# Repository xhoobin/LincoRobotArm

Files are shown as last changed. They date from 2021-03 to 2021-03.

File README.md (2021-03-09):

# tinco桌面机械臂

tinco桌面机械臂设计上易于3D打印，所需零件少。

此仓库包含3D设计图纸、STL 3D打印模型、材料清单、固件

Q群:624506541

## 打印参数

材料 pla 

层高 0.2

填充率 20%

## 样品照片

视频：https://www.bilibili.com/video/BV1D5411N7zT/

视频：https://www.bilibili.com/video/BV18U4y1p7vp

视频：https://www.bilibili.com/video/BV1Gf4y1z7et



## 零件清单

机械部分物料:

轴承钢6806ZZ          (30 * 42 * 7)      3

轴承钢6800ZZ          (10 * 19 * 5)      2

轴承钢6803ZZ           (17 * 26 * 5)     4

轴承钢MR104ZZ        (4 * 10 * 4)       8

2gt同步带                                 1米

m3*18沉孔螺丝                             8     (注意:要用沉孔螺丝)
m3*22螺丝                                   1

m3*10螺丝                                   12

还有胶水(粘轴承用,只在受力小的地方使用胶水,主副臂底座轴承则由打印的螺纹螺帽固定,非常结实)

 电气部分:

 ramps1.4                                      1

a4988驱动板                                  3

mega2560主板                               1 

限位微动开关SS-5GL                       2

12V10A电源                                   1

42步进电机                                    3

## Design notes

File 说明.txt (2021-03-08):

请按给的打印件原本的方向打印(可以保证表面光洁度),安装还是非常容易的 ,后续会推出安装视频,还有调试试频.固件

打印参数
材料 pla 
层高 0.2
填充率 20%

Q群:624506541
linco桌面机械臂

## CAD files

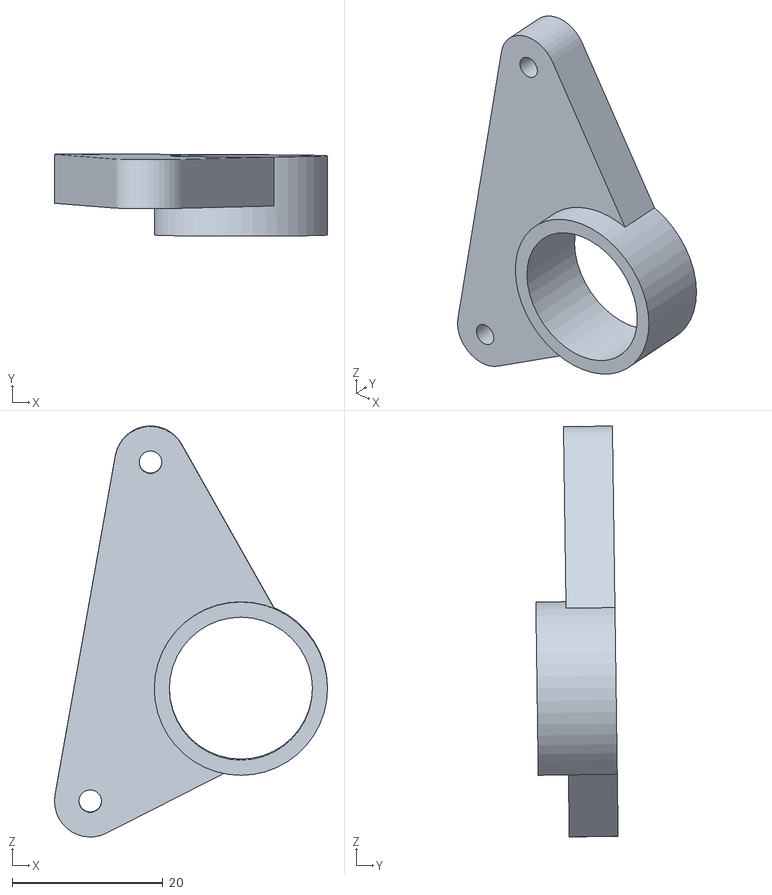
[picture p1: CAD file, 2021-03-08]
打印件/出错/三角.STL
36.2 x 10.9 x 54.6

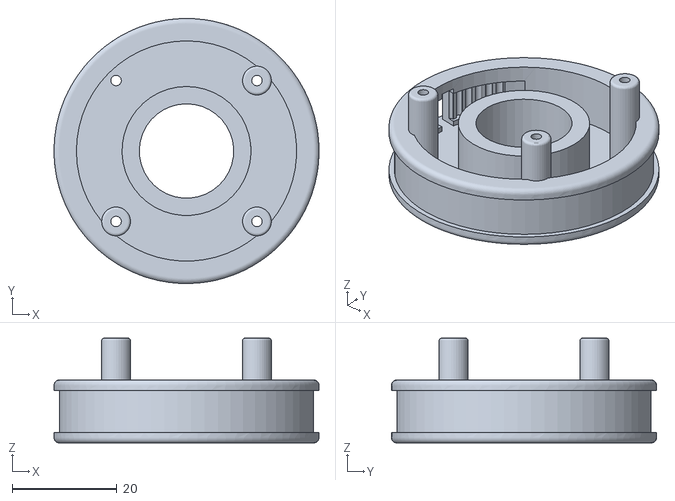
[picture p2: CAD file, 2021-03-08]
打印件/大部件/底轮.STL
50.5 x 50.5 x 20.0

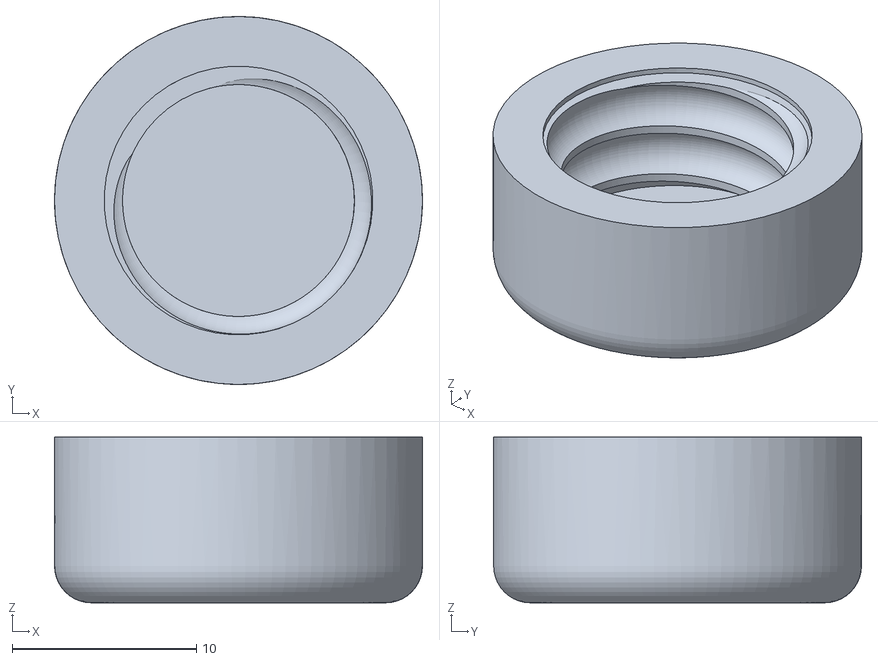
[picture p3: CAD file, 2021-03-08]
打印件/小部件/主臂5.STL
20.0 x 20.0 x 9.00

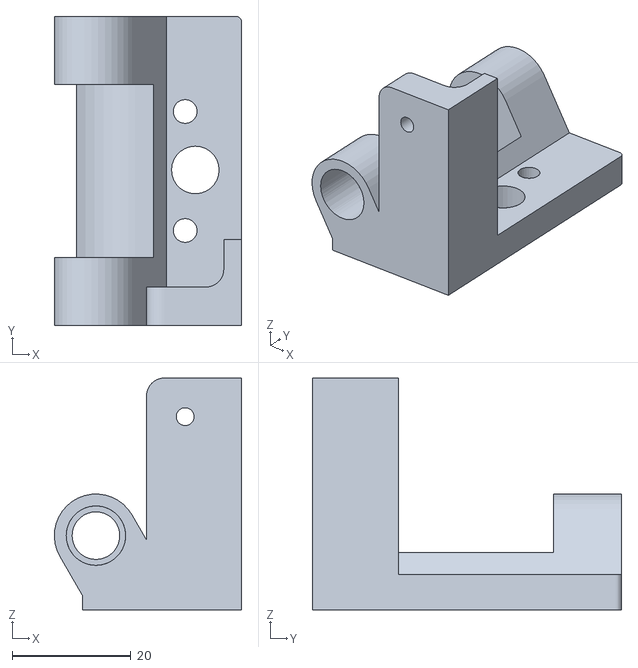
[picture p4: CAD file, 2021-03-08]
打印件/效应器改.STL
31.5 x 52.0 x 39.0

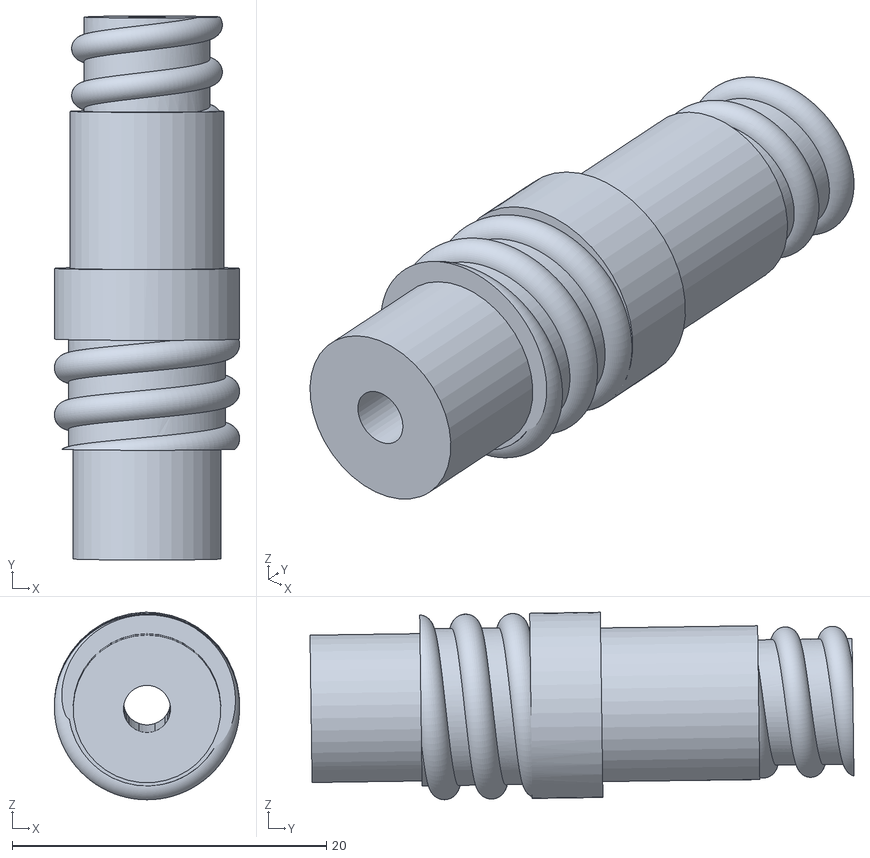
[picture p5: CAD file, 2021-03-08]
打印件/出错/轴.STL
11.8 x 34.6 x 11.9

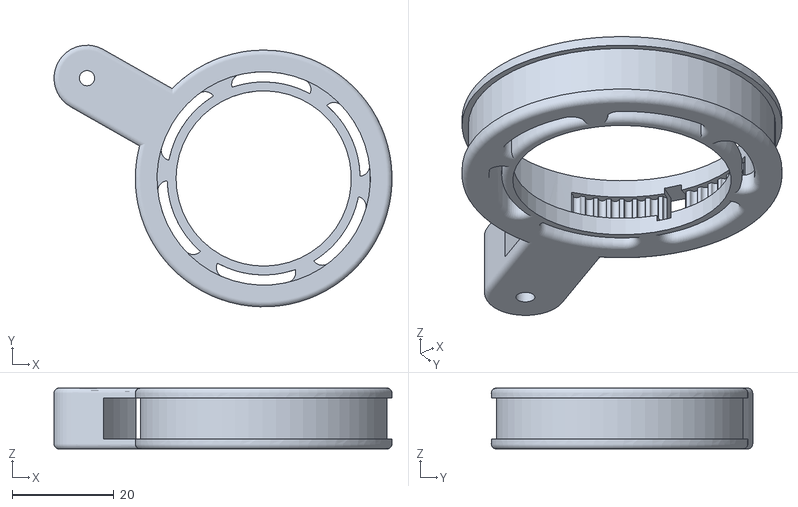
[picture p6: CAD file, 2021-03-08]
打印件/大部件/前轮.STL
66.6 x 51.5 x 12.0

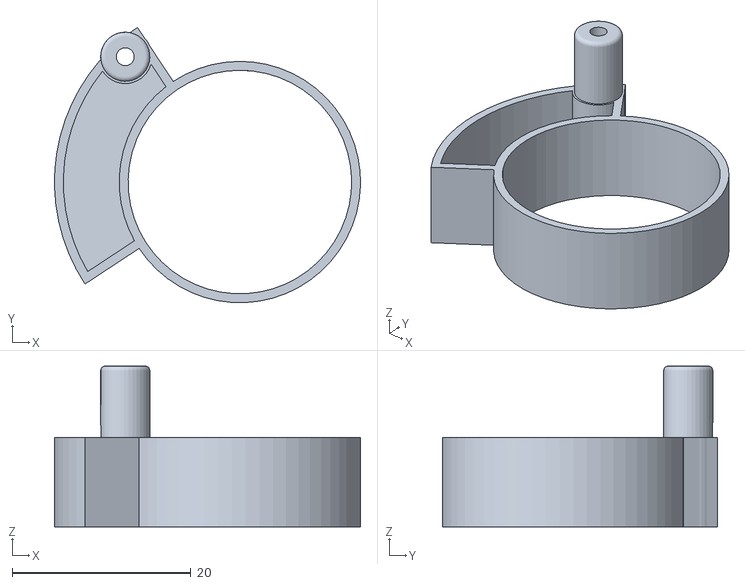
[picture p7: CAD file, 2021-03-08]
打印件/小部件/底轮卡.STL
34.2 x 30.8 x 18.0

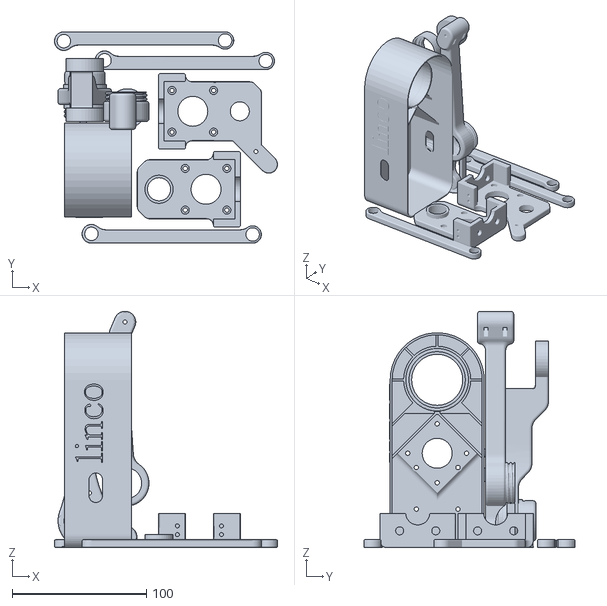
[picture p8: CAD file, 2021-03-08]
打印件/盘2.STL
166.0 x 157.4 x 176.0

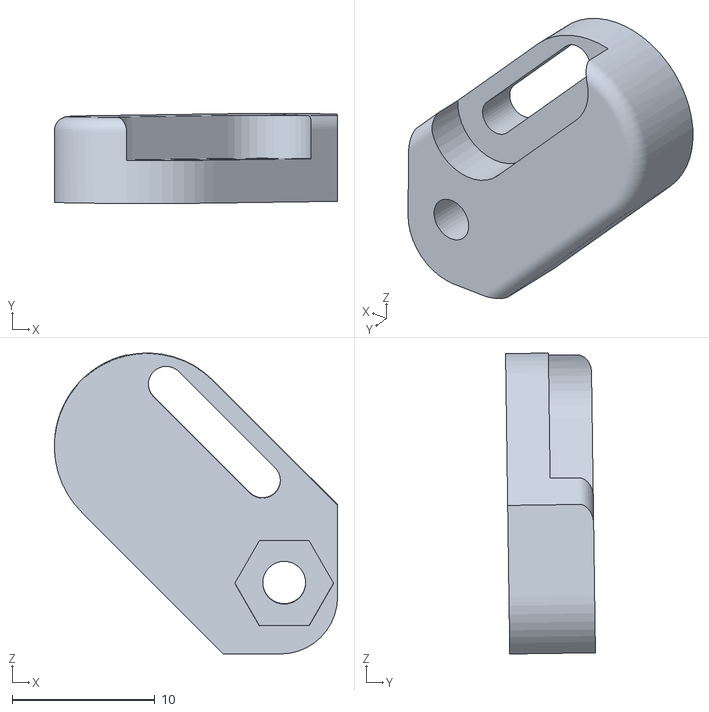
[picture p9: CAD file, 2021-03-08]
打印件/出错/限位固定.STL
19.8 x 6.29 x 21.1

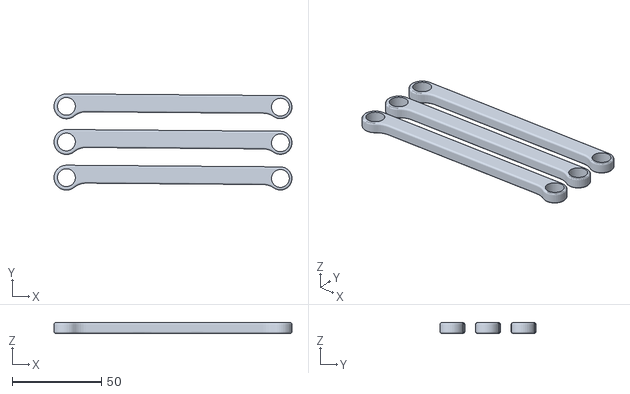
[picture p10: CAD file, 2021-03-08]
打印件/大部件/细臂.STL
133.5 x 54.0 x 6.00

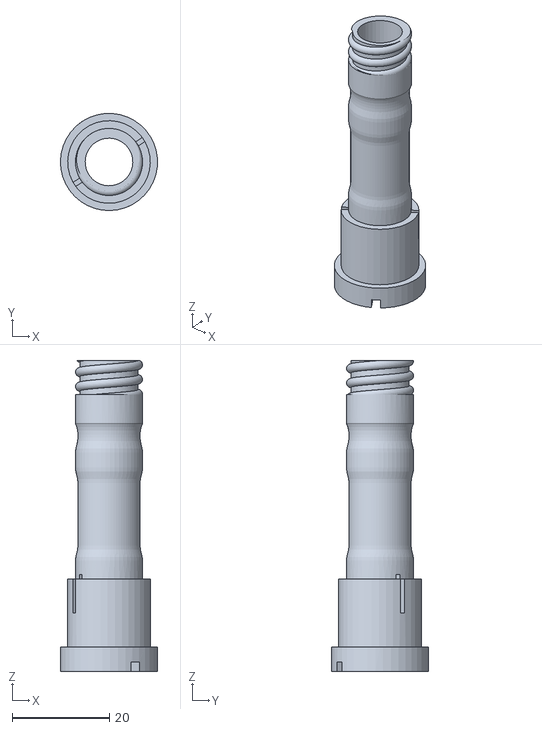
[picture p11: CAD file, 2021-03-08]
打印件/小部件/主臂1.STL
20.0 x 20.0 x 64.0

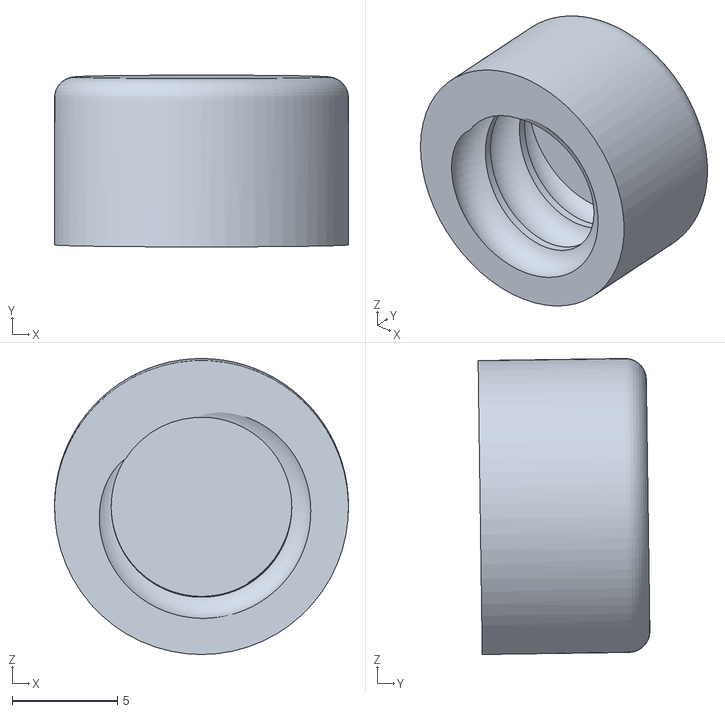
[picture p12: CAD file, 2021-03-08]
打印件/出错/盖子.STL
14.0 x 8.18 x 14.1

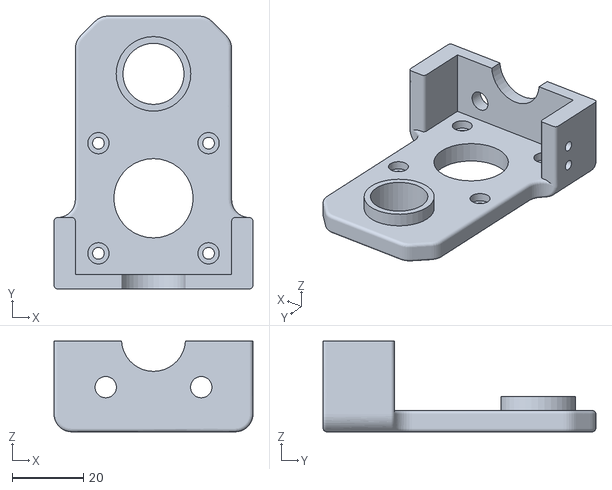
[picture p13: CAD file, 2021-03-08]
打印件/大部件/机身b.STL
56.0 x 76.8 x 25.5

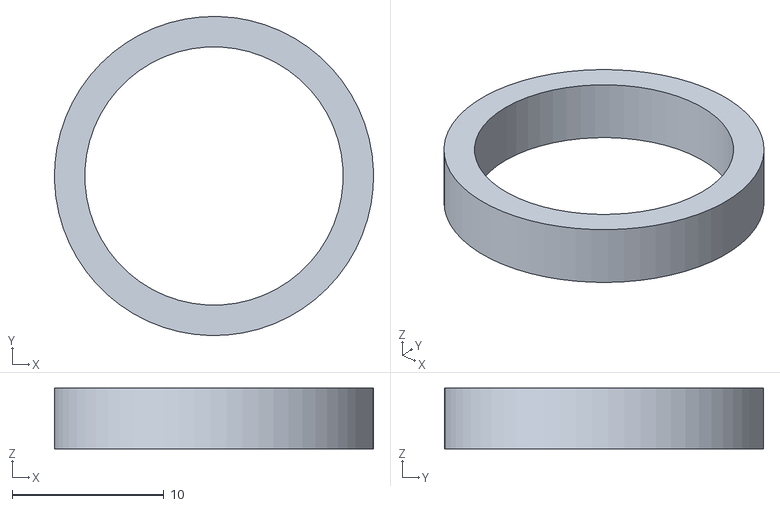
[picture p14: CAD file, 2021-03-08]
打印件/小部件/主臂2.STL
21.0 x 21.0 x 4.00

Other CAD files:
打印件/大部件/机身a.STL
打印件/小部件/底座2.STL
打印件/大部件/效应器.STL
打印件/小部件/前臂6.STL
打印件/大部件/主臂.STL
打印件/大部件/前臂.STL
打印件/大部件/后轮.STL
打印件/大部件/底座.STL
打印件/小部件/三角.STL
打印件/小部件/主臂3.STL
打印件/小部件/主臂4.STL
打印件/小部件/前臂1.STL
打印件/小部件/前臂2.STL
打印件/小部件/前臂3.STL
打印件/小部件/前臂4.STL
打印件/小部件/前臂5.STL
打印件/小部件/前臂7.STL
打印件/小部件/后轮卡.STL
打印件/小部件/底座1.STL
打印件/小部件/底座3.STL
打印件/小部件/底座4.STL
打印件/小部件/零件3.STL
打印件/小部件/零件5.STL

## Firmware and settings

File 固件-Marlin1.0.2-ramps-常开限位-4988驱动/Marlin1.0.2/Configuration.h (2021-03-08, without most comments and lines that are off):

#define CONFIGURATION_H
#include "boards.h"
#define USER_NUMBER " "
#define SCARA
#define scara_segments_per_second 200 //careful, two much will decrease performance...
#define LINKAGE1 120 //mm      Preprocessor cannot handle decimal point...////////////////////////////////////////////////////////////////////////////////////////////////////////////////////////////////////////////////////////////////M366 B120.00 S120.00 C0.00 H0
#define LINKAGE2 120 //mm
#define CENCER_OFFSET 0 //mm
#define HEAD_OFFSET 0 //mm
#define SCARA_OFFSET_X 102.74 //mm
#define SCARA_OFFSET_Y 0.00 //mm
#define SCARA_OFFSET_Z -58 //mm
#define SCARA_RAD2DEG 57.2957795  // to convert RAD to degrees/////////////////////////////////////////////////////////////////////////////////////////////////////////////////////////////////////////////////////////////////////////////M367 X104.31 Y0.00 Z-52.00
#define THETA_HOMING_OFFSET 0	//calculatated from Calibration Guide and command M360 / M114 see picture in http://reprap.harleystudio.co.za/?page_id=1073
#define PSI_HOMING_OFFSET 0  // calculatated from Calibration Guide and command M364 / M114 see picture in http://reprap.harleystudio.co.za/?page_id=1073
#define MANUAL_HOME_POS_X 114.13/////////////////////////////////////////////////////////////////////////////////////////////////////////////////////////////////////////////////////////////////////////////////////////////////////////////////M368 X113.08 Y4.08 Z0.00
#define MANUAL_HOME_POS_Y 4.51
#define MANUAL_HOME_POS_Z 0
#define PRINTABLE_RADIUS_MAX 320
#define PRINTABLE_RADIUS_MIN 80
#define STRING_VERSION_CONFIG_H __DATE__ " " __TIME__ // build date and time
#define STRING_CONFIG_H_AUTHOR "(none, default config)" // Who made the changes.
#define SERIAL_PORT 0
#define BAUDRATE 115200
  #define MOTHERBOARD BOARD_RAMPS_13_EFB //BOARD_MELZI
#define CUSTOM_MENDEL_NAME "linco-arm"
#define EXTRUDERS 1
#define POWER_SUPPLY 1
#define SUPPORT_LASER
#define TEMP_SENSOR_0 0
#define TEMP_SENSOR_1 0
#define TEMP_SENSOR_2 0
#define TEMP_SENSOR_BED 0
#define MAX_REDUNDANT_TEMP_SENSOR_DIFF 10
#define TEMP_RESIDENCY_TIME 3  // (seconds)
#define TEMP_HYSTERESIS 2       // (degC) range of +/- temperatures considered "close" to the target one
#define TEMP_WINDOW     1       // (degC) Window around target to start the residency timer x degC early.
#define HEATER_0_MINTEMP 5
#define HEATER_1_MINTEMP 5
#define HEATER_2_MINTEMP 5
#define BED_MINTEMP 5
#define HEATER_0_MAXTEMP 275
#define HEATER_1_MAXTEMP 275
#define HEATER_2_MAXTEMP 275
#define BED_MAXTEMP 150
#define EXTRUDER_WATTS (2*2/5.9) //  P=I^2/R
#define BED_WATTS (5.45*5.45/2.2)      // P=I^2/R
#define PIDTEMP
#define BANG_MAX 255 // limits current to nozzle while in bang-bang mode; 255=full current
#define PID_MAX 255 // limits current to nozzle while PID is active (see PID_FUNCTIONAL_RANGE below); 255=full current
  #define PID_FUNCTIONAL_RANGE 20 // If the temperature difference between the target temperature and the actual temperature
  #define PID_INTEGRAL_DRIVE_MAX 255  //limit for the integral term
  #define K1 0.95 //smoothing factor within the PID
  #define PID_dT ((OVERSAMPLENR * 8.0)/(F_CPU / 64.0 / 256.0)) //sampling period of the temperature routine
    #define  DEFAULT_Kp 24.5
    #define  DEFAULT_Ki 1.72
    #define  DEFAULT_Kd 87.73
#define PIDTEMPBED
#define BED_LIMIT_SWITCHING
#define MAX_BED_POWER 255 // limits duty cycle to bed; 255=full current
    #define  DEFAULT_bedKp 630.14
    #define  DEFAULT_bedKi 121.71
    #define  DEFAULT_bedKd 815.64
#define PREVENT_LENGTHY_EXTRUDE
#define EXTRUDE_MINTEMP 150
#define EXTRUDE_MAXLENGTH (X_MAX_LENGTH+Y_MAX_LENGTH) //prevent extrusion of very large distances.
#define ENDSTOPPULLUPS // Comment this out (using // at the start of the line) to disable the endstop pullup resistorsM368
  #define ENDSTOPPULLUP_XMAX
  #define ENDSTOPPULLUP_YMAX
  #define ENDSTOPPULLUP_ZMAX
  #define ENDSTOPPULLUP_XMIN
  #define ENDSTOPPULLUP_YMIN
  #define ENDSTOPPULLUP_ZMIN
const bool X_MIN_ENDSTOP_INVERTING = true; // set to true to invert the logic of the endstop.
const bool Y_MIN_ENDSTOP_INVERTING = true; // set to true to invert the logic of the endstop.
const bool Z_MIN_ENDSTOP_INVERTING = true; // set to true to invert the logic of the endstop.
const bool X_MAX_ENDSTOP_INVERTING = true; // set to true to invert the logic of the endstop.
const bool Y_MAX_ENDSTOP_INVERTING = true; // set to true to invert the logic of the endstop.
const bool Z_MAX_ENDSTOP_INVERTING = true; // set to true to invert the logic of the endstop.
#if defined(COREXY) && !defined(DISABLE_MAX_ENDSTOPS)
  #define DISABLE_MAX_ENDSTOPS
#endif
#define X_ENABLE_ON 0
#define Y_ENABLE_ON 0
#define Z_ENABLE_ON 0
#define E_ENABLE_ON 0 // For all extruders
#define DISABLE_X false
#define DISABLE_Y false
#define DISABLE_Z false
#define DISABLE_E false // For all extruders
#define DISABLE_INACTIVE_EXTRUDER true //disable only inactive extruders and keep active extruder enabled
#define INVERT_X_DIR true    // for Mendel set to false, for Orca set to true
#define INVERT_Y_DIR false    // for Mendel set to true, for Orca set to false
#define INVERT_Z_DIR false     // for Mendel set to false, for Orca set to true
#define INVERT_E0_DIR true   // for direct drive extruder v9 set to true, for geared extruder set to false
#define INVERT_E1_DIR false    // for direct drive extruder v9 set to true, for geared extruder set to false
#define INVERT_E2_DIR false   // for direct drive extruder v9 set to true, for geared extruder set to false
#define X_HOME_DIR 1
#define Y_HOME_DIR 1
#define Z_HOME_DIR 1
#define min_software_endstops false // If true, axis won't move to coordinates less than HOME_POS.
#define max_software_endstops false  // If true, axis won't move to coordinates greater than the defined lengths below.
#define min_software_angle_endstops true
#define max_software_angle_endstops true
#define X_MAX_ANGLE 180/////////////////////////////////////////////////////////////////////////////////////////////////////////////////////////////////*******************************************************可能是角度范围
#define X_MIN_ANGLE 0
#define Y_MAX_ANGLE 90
#define Y_MIN_ANGLE -90
#define X_MAX_POS 200/////////////////////////////////////////////////////////////////////////////////////////////////////////////////////////////////*******************************************************配置打印机最大和最小坐标，单位是mm
#define X_MIN_POS 0
#define Y_MAX_POS 200
#define Y_MIN_POS 0
#define Z_MAX_POS 225
#define Z_MIN_POS MANUAL_Z_HOME_POS
#define X_MAX_LENGTH (X_MAX_POS - X_MIN_POS)
#define Y_MAX_LENGTH (Y_MAX_POS - Y_MIN_POS)
#define Z_MAX_LENGTH (Z_MAX_POS - Z_MIN_POS)
#define MANUAL_HOME_POSITIONS  // If defined, MANUAL_*_HOME_POS below will be used
#define MANUAL_X_HOME_POS -22.
#define MANUAL_Y_HOME_POS -52.
#define MANUAL_Z_HOME_POS 0.1  // Distance between nozzle and print surface after homing.
#define NUM_AXIS 4 // The axis order in all axis related arrays is X, Y, Z, E
#define HOMING_FEEDRATE {30*60, 30*60, 30*60, 0}  // set the homing speeds (mm/min)/////////////////////////////////////////////////////////////////////////////////////////////////////////////////////////////////////////////////////home速度
#define DEFAULT_AXIS_STEPS_PER_UNIT  {35.56,35.56,35.56,92.43} //{71.12,71.12,71.12,184.86}//{35.56,35.56,35.56,92.43}  // default steps per unit for SCARA///////////////////////////////////////8825//M92 X71.12 Y71.12 Z71.12 E184.86///////////////////////////4988///M92 X35.56 Y35.56 Z35.56 E92.43
#define DEFAULT_MAX_FEEDRATE          {5000, 5000, 5000,5000}    // (mm/sec)
#define DEFAULT_MAX_ACCELERATION      {9000,9000,9000,9000}    // X, Y, Z, E maximum start speed for accelerated moves. E default values are good for Skeinforge 40+, for older versions raise them a lot.
#define DEFAULT_ACCELERATION          3000   // X, Y, Z and E max acceleration in mm/s^2 for printing moves/////////////////////////////////////////////////////////////////////////////////////////////////////////////////////////////////绝对速度
#define DEFAULT_RETRACT_ACCELERATION  3000  // X, Y, Z and E max acceleration in mm/s^2 for retracts
#define DEFAULT_XYJERK                30    // (mm/sec)
#define DEFAULT_ZJERK                30    // (mm/sec)
#define DEFAULT_EJERK                 3    // (mm/sec)
#define EEPROM_CHITCHAT
#define PLA_PREHEAT_HOTEND_TEMP 180
#define PLA_PREHEAT_HPB_TEMP 70
#define PLA_PREHEAT_FAN_SPEED 255   // Insert Value between 0 and 255
#define ABS_PREHEAT_HOTEND_TEMP 240
#define ABS_PREHEAT_HPB_TEMP 100
#define ABS_PREHEAT_FAN_SPEED 255   // Insert Value between 0 and 255
#define SOFT_PWM_SCALE 0
#define FILAMENT_SENSOR_EXTRUDER_NUM  0  //The number of the extruder that has the filament sensor (0,1,2)
#define MEASUREMENT_DELAY_CM      14  //measurement delay in cm.  This is the distance from filament sensor to middle of barrel
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

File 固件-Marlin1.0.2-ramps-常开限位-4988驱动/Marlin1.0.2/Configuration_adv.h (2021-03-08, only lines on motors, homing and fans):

#define CONTROLLERFAN_PIN -1 //Pin used for the fan to cool controller (-1 to disable)
#define EXTRUDER_0_AUTO_FAN_PIN   -1
#define EXTRUDER_1_AUTO_FAN_PIN   -1
#define EXTRUDER_2_AUTO_FAN_PIN   -1
  #define X_HOME_POS MANUAL_X_HOME_POS
  #define Y_HOME_POS MANUAL_Y_HOME_POS
  #define Z_HOME_POS MANUAL_Z_HOME_POS
#define X_HOME_RETRACT_MM 3
#define Y_HOME_RETRACT_MM 3
#define Z_HOME_RETRACT_MM 3
	#define QUICK_HOME //SCARA needs Quickhome
#define MICROSTEP1 LOW,LOW
#define MICROSTEP2 HIGH,LOW
#define MICROSTEP4 LOW,HIGH
#define MICROSTEP8 HIGH,HIGH
#define MICROSTEP16 HIGH,HIGH
#define MICROSTEP_MODES {16,16,16,16,16} // [1,2,4,8,16]
#define DIGIPOT_MOTOR_CURRENT {135,135,135,135,135} // Values 0-255 (RAMBO 135 = ~0.75A, 185 = ~1A)
#define DIGIPOT_I2C_MOTOR_CURRENTS {1.0, 1.0, 1.0, 1.0, 1.0, 1.0, 1.0, 1.0}

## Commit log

2021-03-08 添加全部资料
    [Configuration.h, Configuration_adv.h, Robotic_Arm_Finger.stl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]
2021-03-09 添加readme
2021-03-09 修改文件目录、删除不需要的文件
    [Robotic_Arm_Finger.stl, Robotic_Arm_Finger_Pad.stl, Robotic_Arm_Forward_Hinge_Arm.stl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]
2021-03-09 修改readme
2021-03-09 规整文件目录
    [盘2.STL]
2021-03-09 Update README.md
    添加视频链接
